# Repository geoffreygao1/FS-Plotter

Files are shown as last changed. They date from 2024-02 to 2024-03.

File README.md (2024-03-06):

# _F.S. PLOTTER_
**By: Geoffrey Gao**

<p align="center">

</p>

_An attachment for the [Ender 3](https://www.creality.com/products/ender-3-3d-printer) 3D Printer that allows for 2D Plotter functionality. This project was intended to allow for printing onto non-standard materials/objects. Included are the designs for the following:_

### Plotter

A spring loaded fixture to designed to hold a pen in place on the Ender 3 X-Carriage. Can be used with any writing utensil (up to 15mm diameter) and other tools (e.g., scribers, engravers, etc.)

<p align="center">
 <span>
  
</span>
</p>

### Cassette Tape Fixture
 A simple fixture to allow one to print directly onto a cassette tape. This was intended as a cheaper alternative to pad printing, with a better finish than printout tape labels. For best results, use an oil ink based pen for printing to prevent smearing. 

  <p align="center">
  <span>     
    </span>
  </p>

## Examples

Showcasing prints on paper, wood, fabric, cassette, and engraving on acrylic:
<p align="center">
<span>





</span>
</p>

## Getting Started

### Design Files
This repo contains design files for the main Plotter assembly and the Cassette Tape Fixture. The plotter was designed to be compatible with the Ender 3 X carriage. You can 3D print the STL files without the need for supports using your preferred slicer settings. There are also design templates included for use with the cassette fixture.

### PrusaSlicer Settings
The PrusaSlicer settings profile I use to generate the plotter GCode is included. PrusaSlicer is a free slicer available [here](https://www.prusa3d.com/en/page/prusaslicer_424/). You can learn how to import profile settings [here](https://help.prusa3d.com/article/how-to-import-and-export-custom-profiles-in-prusaslicer_382766). The input into PrusaSlicer will be the SVG file formats of your design.

### Instructions
Contains PDFs with instructions on how to assemble, install, and use the plotter. Also includes a disassembly guide on how to remove the existing hotend on the Ender 3 printer.

## Setup/Installation Requirements
### Tools
The following tools are needed to build the F.S. Plotter and Cassette Fixture:
*  Ender 3 3D Printer
*  Hex Drivers
*  M2, M3, M4 Thread Taps
*  Computer capable of running PrusaSlicer

### Materials
The following materials are needed to build the F.S. Plotter and Cassette Fixture 
_(Note the springs and screws are purchased in a kit but only specific ones are needed. See assembly instructions for details)_:
*  PLA to print the parts
*  [40mm Linear Rail](https://www.aliexpress.us/item/2251832805844953.html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)
* [Metric Screw Kit](https://www.amazon.com/gp/product/B07K141VFD/ref=ppx_yo_dt_b_search_asin_title?ie=UTF8&psc=1)
* [Extension Spring Kit](https://www.amazon.com/dp/B0CFRF42LQ?psc=1&ref=ppx_yo2ov_dt_b_product_details)
* [Compression Spring Kit](https://www.amazon.com/Dianrui-Compression-Assortment-Mechanical-K-P-051-300/dp/B0BVTDP29W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)

If individual parts are purchased separately (via Aliexpress), both assemblies can be built for around $30!

## Assembly/Usage Instructions
_Please see the PDFs included in the [Instructions Folder](https://github.com/geoffreygao1/Plotter/tree/main/Instructions) for assembly and usage instructions_

## Notes

This is still a work in progress so please check regularly for updates! Special thanks to Jake C. for allowing me to borrow his Ender 3!

## License
Copyright (c) _2024_  _Geoffrey Gao_  
_Not for commercial use_

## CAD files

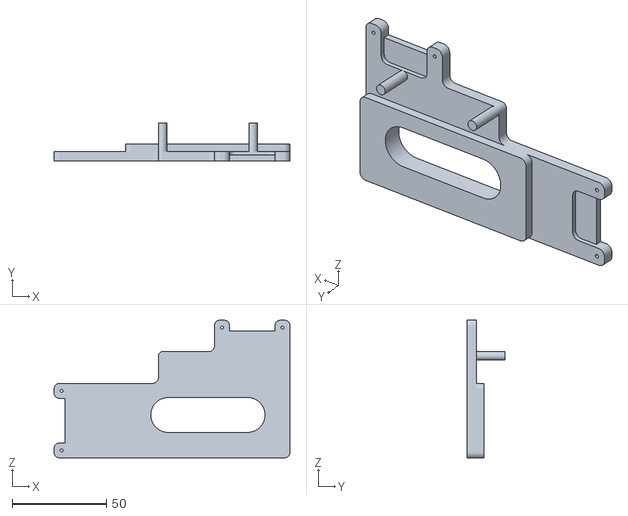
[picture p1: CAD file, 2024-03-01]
Design Files/Cassette Mount/Base, Cassette Fixture, V3.STL
125.0 x 20.0 x 73.0

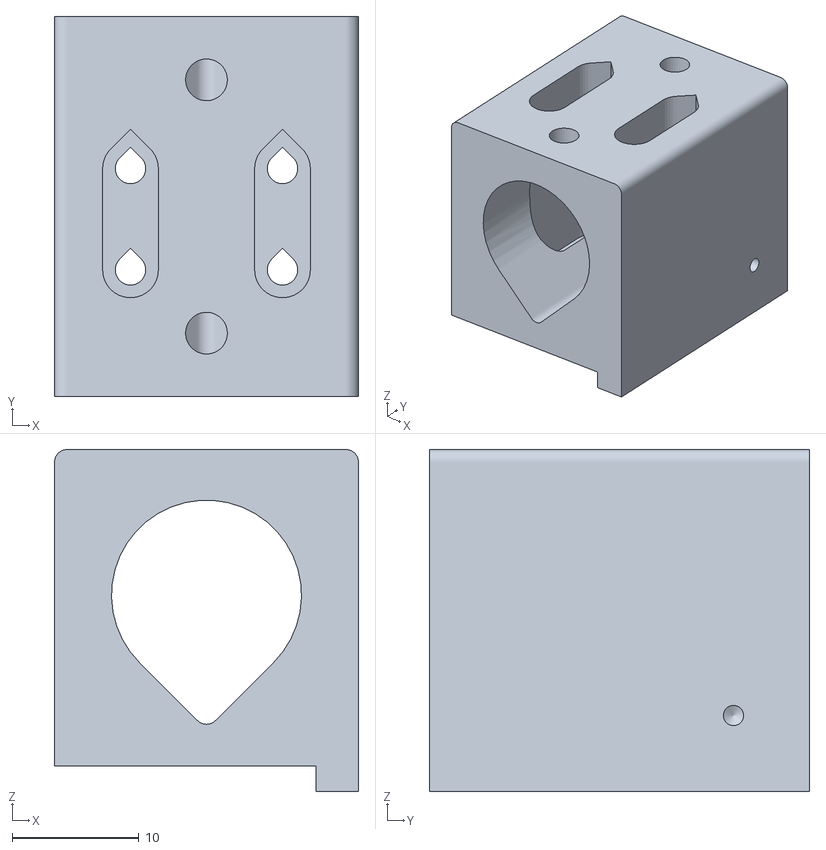
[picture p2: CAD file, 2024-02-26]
Design Files/Plotter/Carriage Mount.STL
24.0 x 30.0 x 27.0

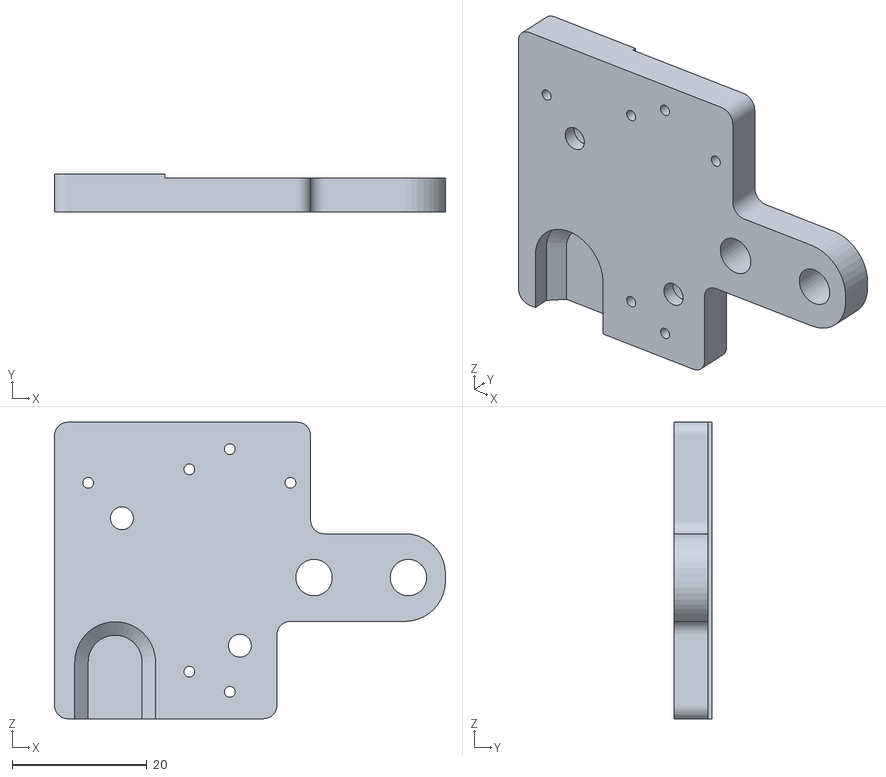
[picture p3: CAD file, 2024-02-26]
Design Files/Plotter/Pen Holder.STL
58.0 x 5.60 x 44.0

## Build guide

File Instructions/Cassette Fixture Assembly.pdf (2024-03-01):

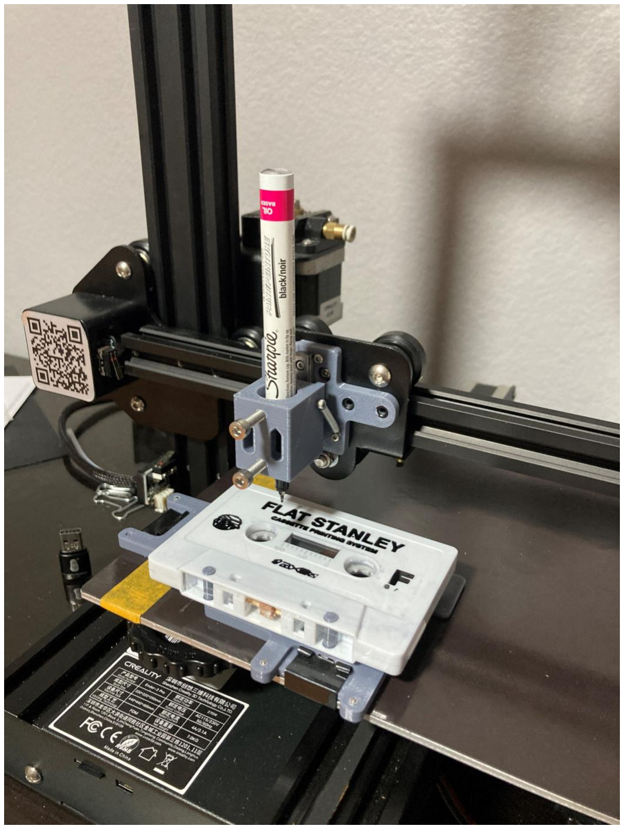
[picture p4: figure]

# Cassette Tape Fixture

Assembly / Installation Guide

By: Geoffrey Gao
02/2024

## Bill of Materials

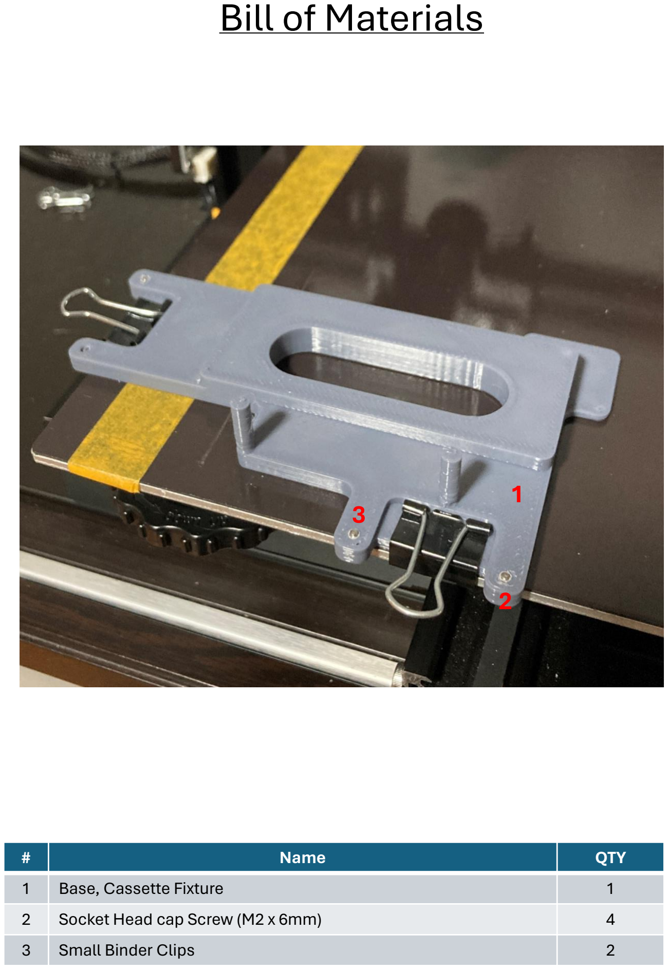
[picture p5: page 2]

# | Name | QTY

1 | Base, Cassette Fixture | 1
2 | Socket Head cap Screw (M2 x 6mm) | 4
3 | Small Binder Clips | 2

1

2

3

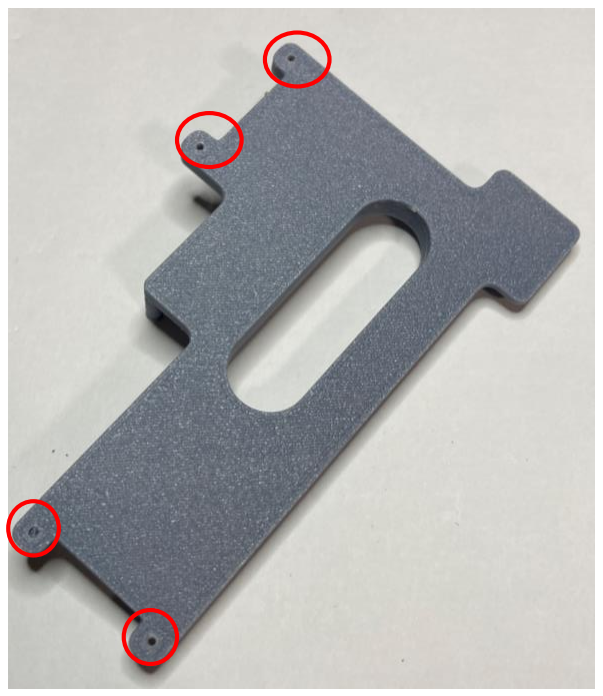
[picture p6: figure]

1. Tap the noted holes with an M2 Tap.

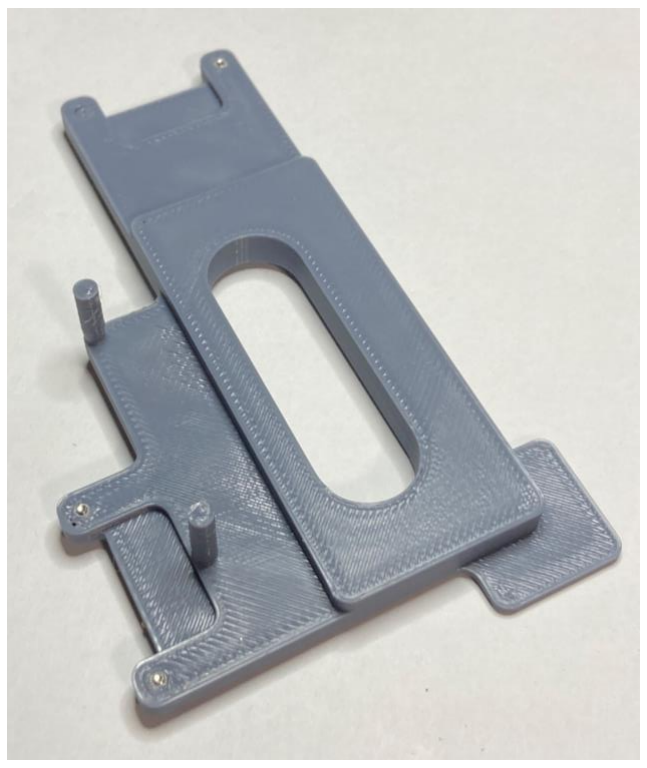
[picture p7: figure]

2. Install M2 x 6mm Screws in the holes that were just tapped from the bottom

## Assembly Instructions

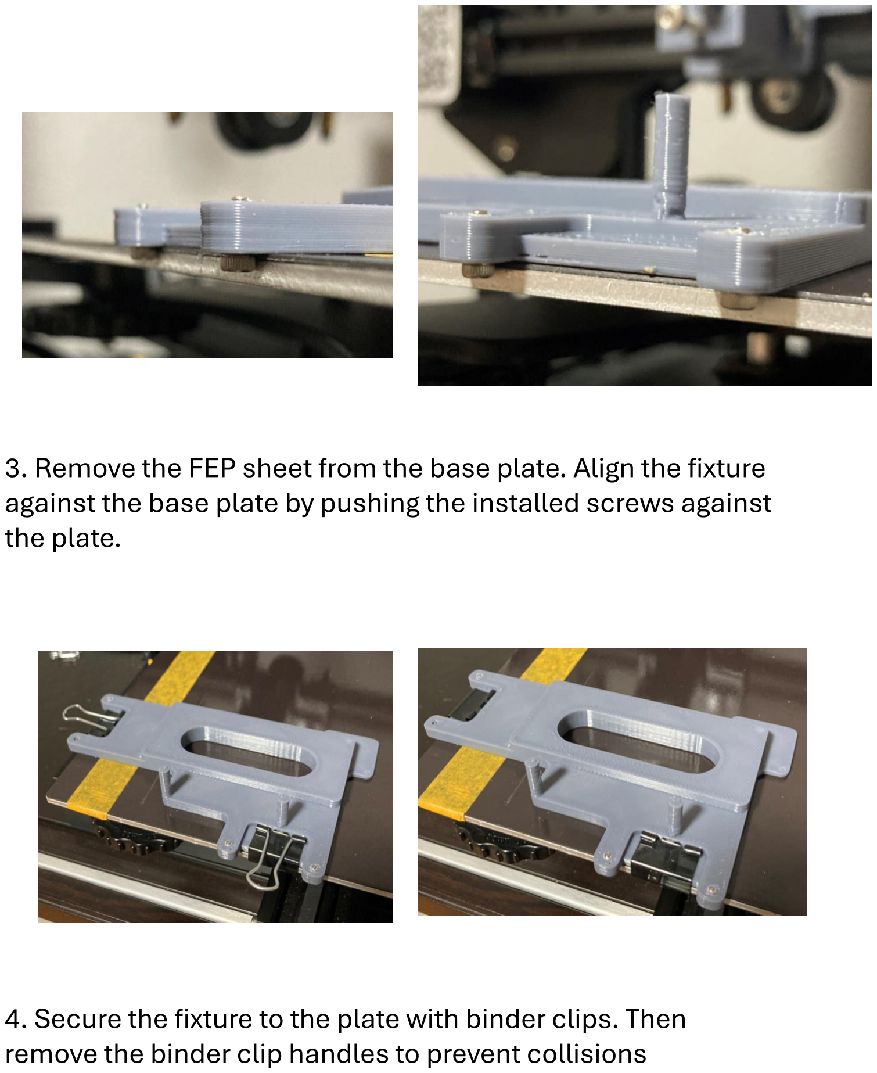
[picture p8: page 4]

3. Remove the FEP sheet from the base plate. Align the fixture against the base plate by pushing the installed screws against the plate.
4. Secure the fixture to the plate with binder clips. Then remove the binder clip handles to prevent collisions

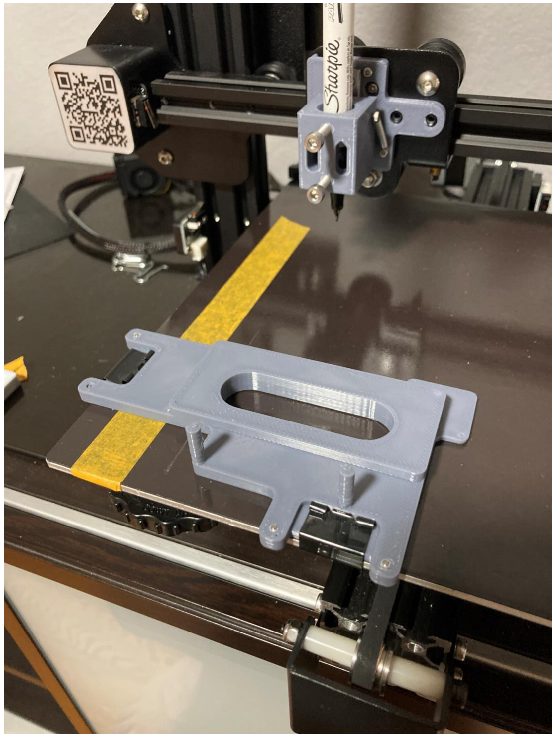
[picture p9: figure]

Installation is complete!

## Setup Instructions

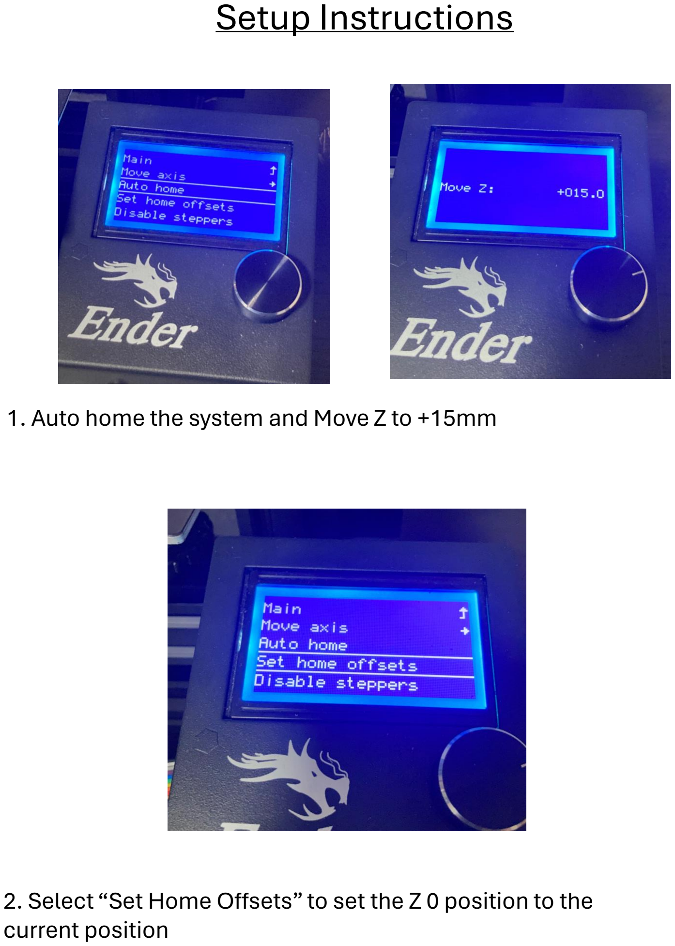
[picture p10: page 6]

1. Auto home the system and Move Z to +15mm
2. Select “Set Home Offsets” to set the Z 0 position to the current position

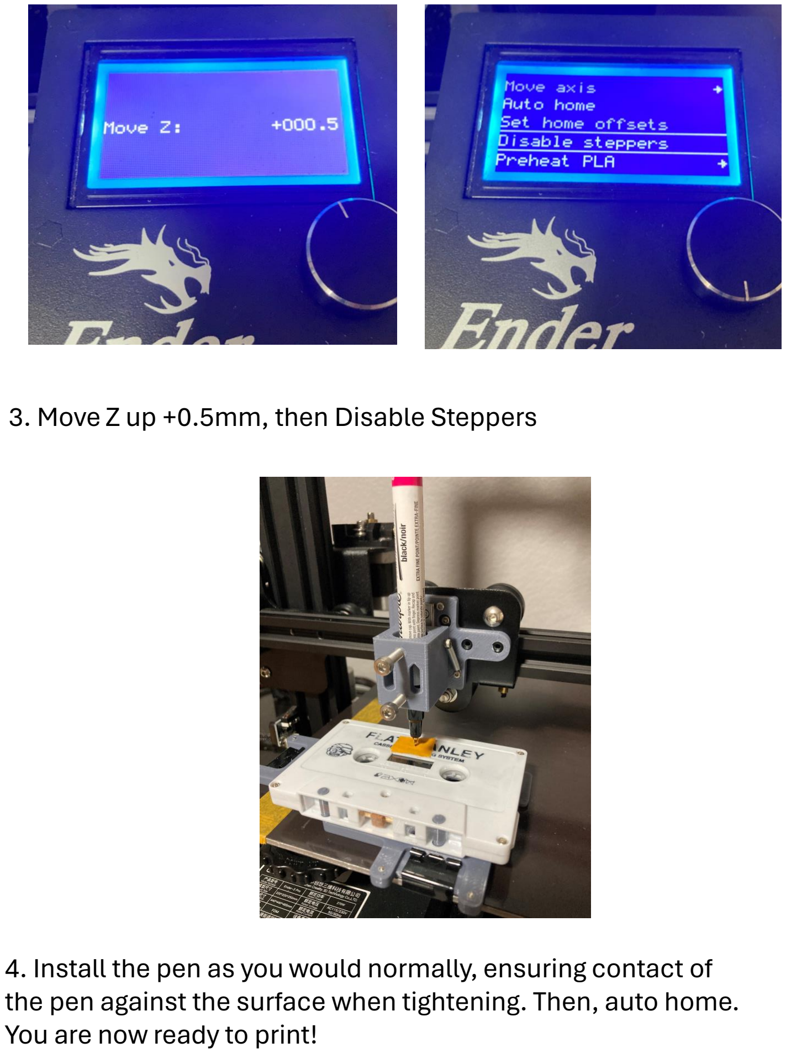
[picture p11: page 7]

3. Move Z up +0.5mm, then Disable Steppers
4. Install the pen as you would normally, ensuring contact of the pen against the surface when tightening. Then, auto home. You are now ready to print!

## Gcode Generation

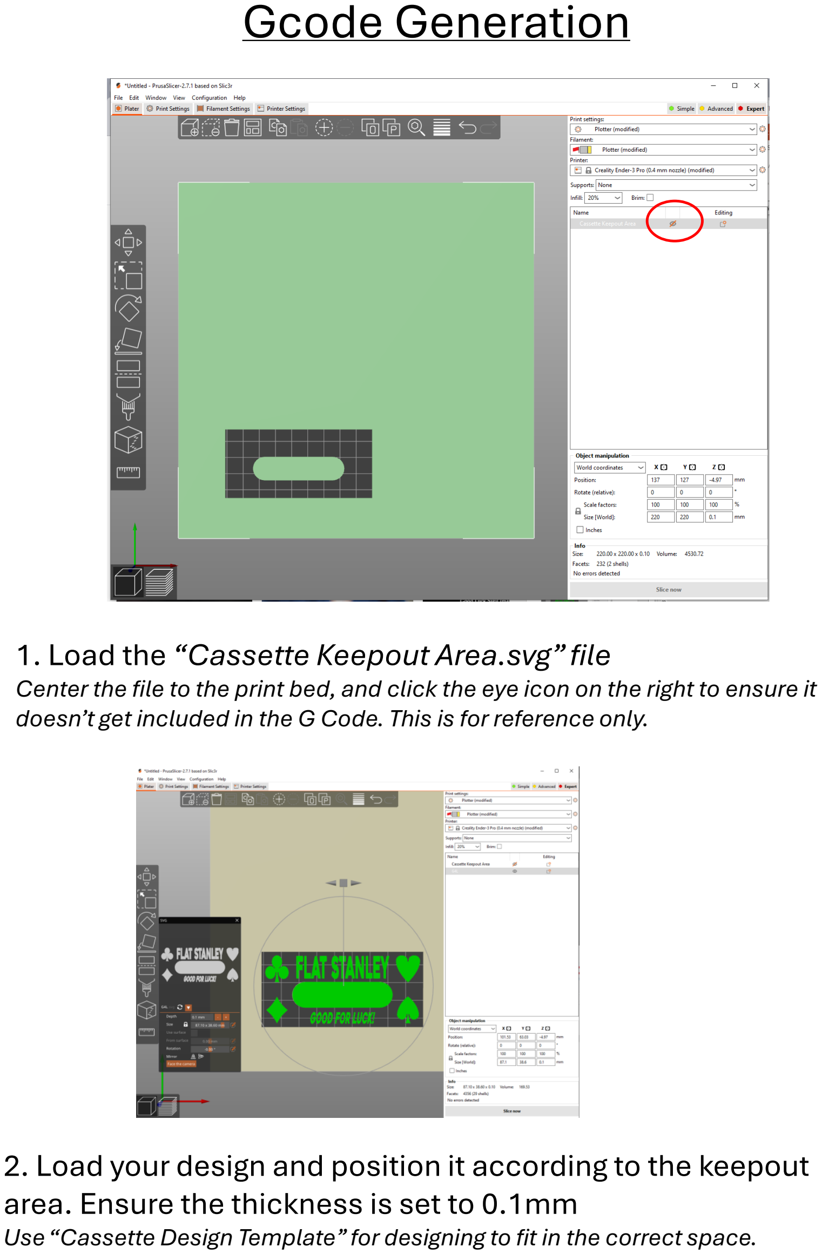
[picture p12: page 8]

1. Load the “Cassette Keepout Area.svg” file
Center the file to the print bed, and click the eye icon on the right to ensure it doesn’t get included in the G Code. This is for reference only.
2. Load your design and position it according to the keepout area. Ensure the thickness is set to 0.1mm
Use “Cassette Design Template” for designing to fit in the correct space.

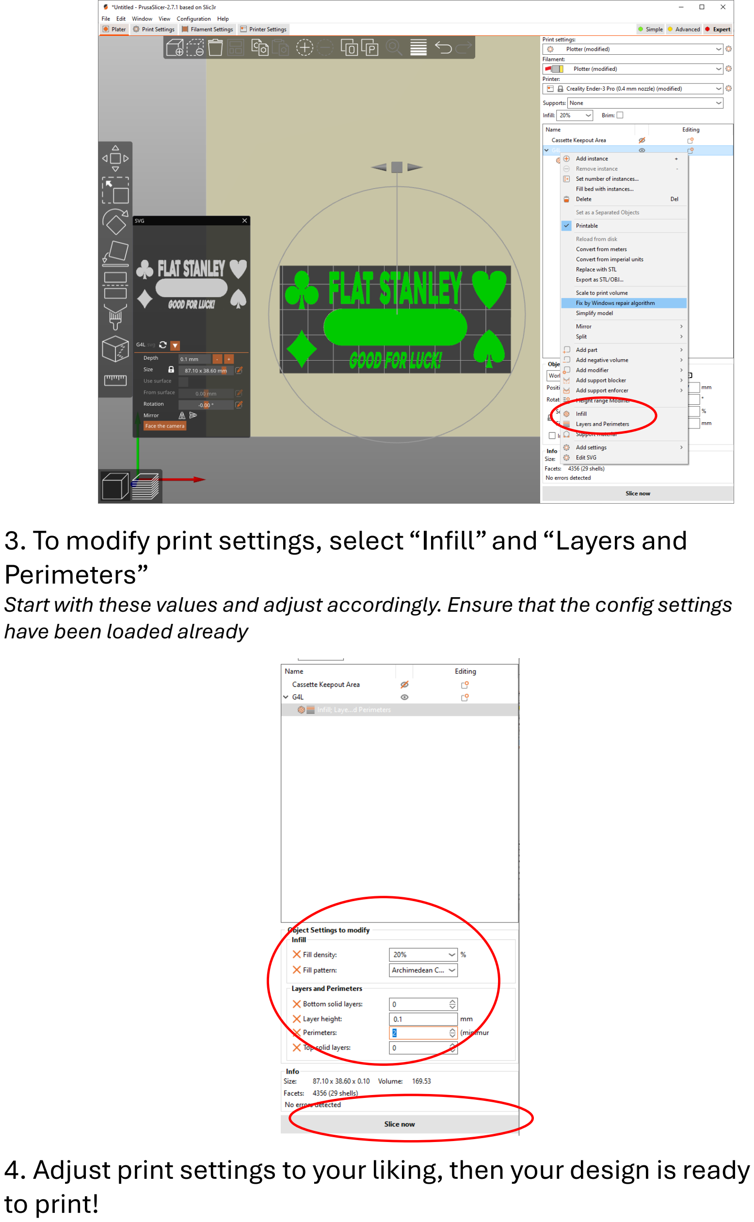
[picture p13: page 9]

3. To modify print settings, select “Infill” and “Layers and Perimeters”
Start with these values and adjust accordingly. Ensure that the config settings have been loaded already
4. Adjust print settings to your liking, then your design is ready to print!

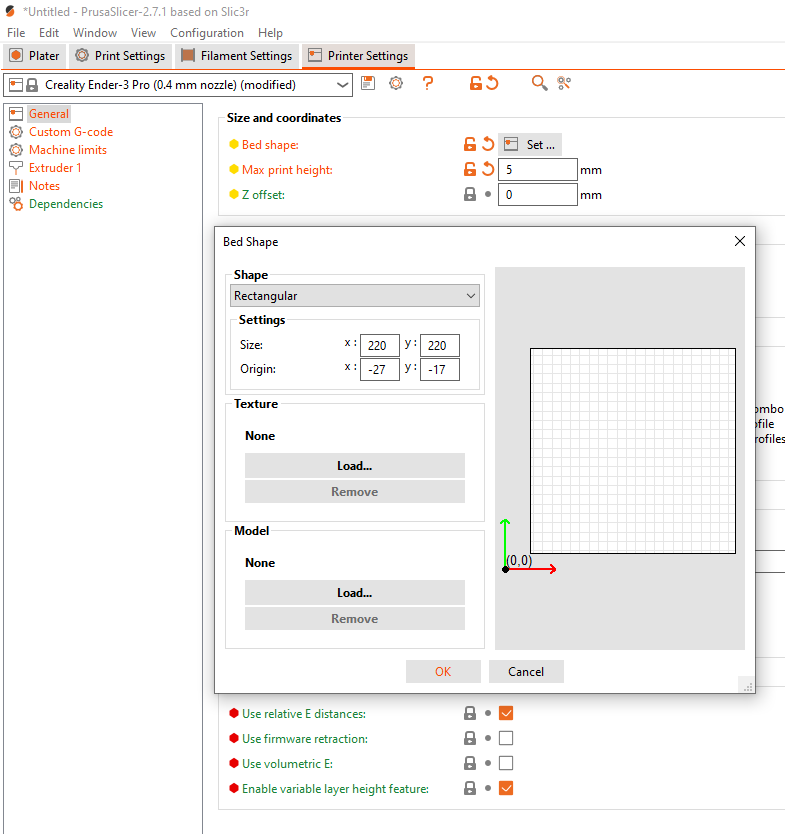
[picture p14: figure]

If you are noticing that the print is not aligned to the intended coordinates, you may have to adjust the XY offset in Prusaslicer
- In PrusaSlicer , Printer Settings, Bed Shape, and adjust the Origin XY values
- These values are related to the size of the pen being used, so adjust accordingly

Troubleshooting:

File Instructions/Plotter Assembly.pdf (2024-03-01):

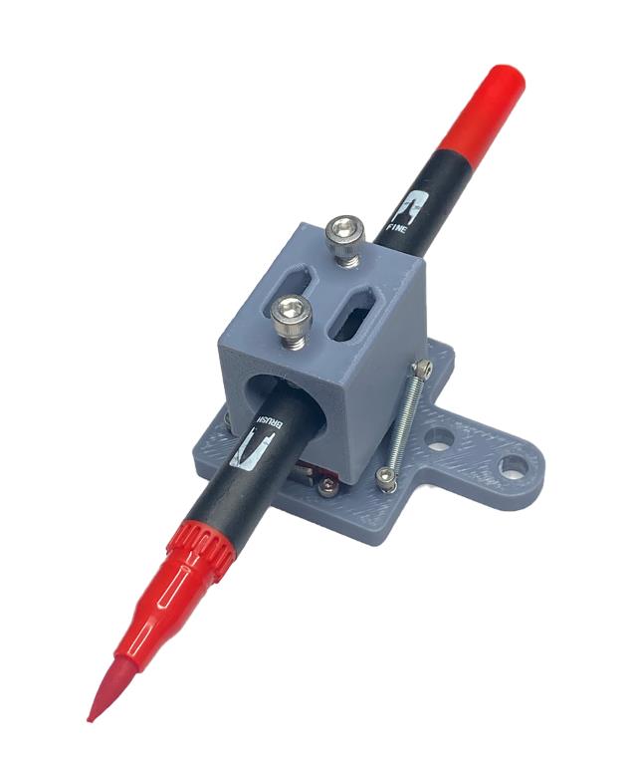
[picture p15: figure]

# FS Plotter

## Assembly / Installation Guide

By: Geoffrey Gao
02/2024

# Bill of Materials

3

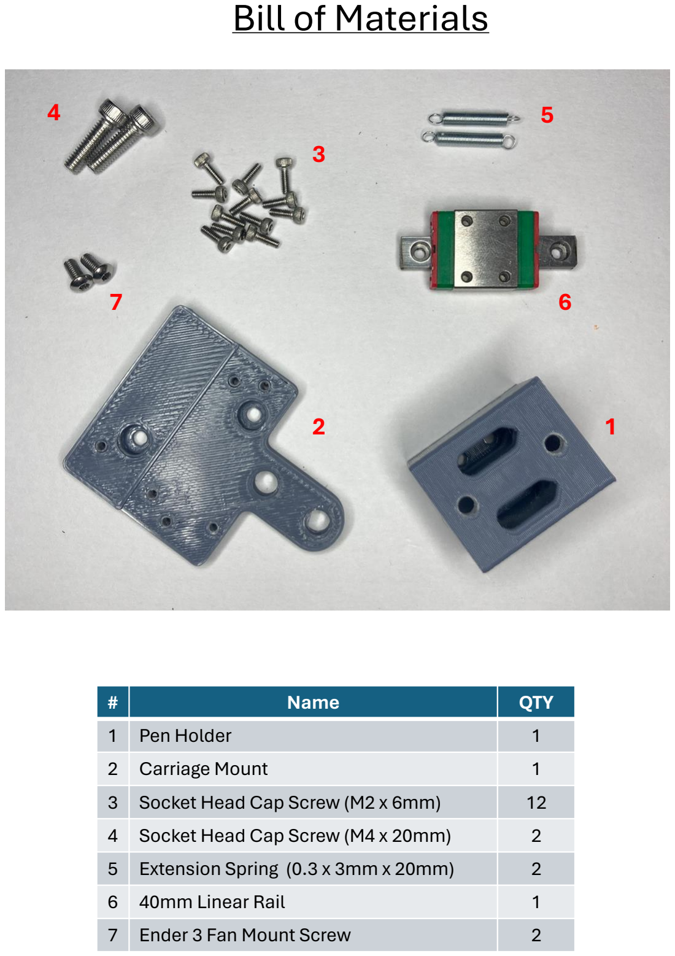
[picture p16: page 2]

# | Name | QTY

1 | Pen Holder | 1
2 | Carriage Mount | 1
3 | Socket Head Cap Screw (M2 x 6mm) | 12
4 | Socket Head Cap Screw (M4 x 20mm) | 2
5 | Extension Spring (0.3 x 3mm x 20mm) | 2
6 | 40mm Linear Rail | 1
7 | Ender 3 Fan Mount Screw | 2

2 1

4 5

7 6

# Assembly Instructions

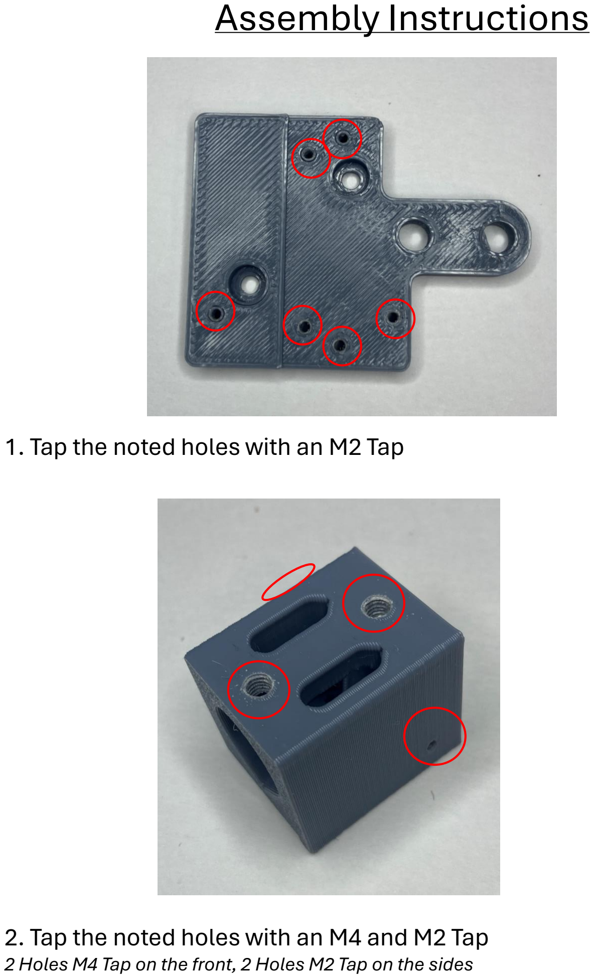
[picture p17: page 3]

### 1. Tap the noted holes with an M2 Tap

### 2. Tap the noted holes with an M4 and M2 Tap

2 Holes M4 Tap on the front, 2 Holes M2 Tap on the sides

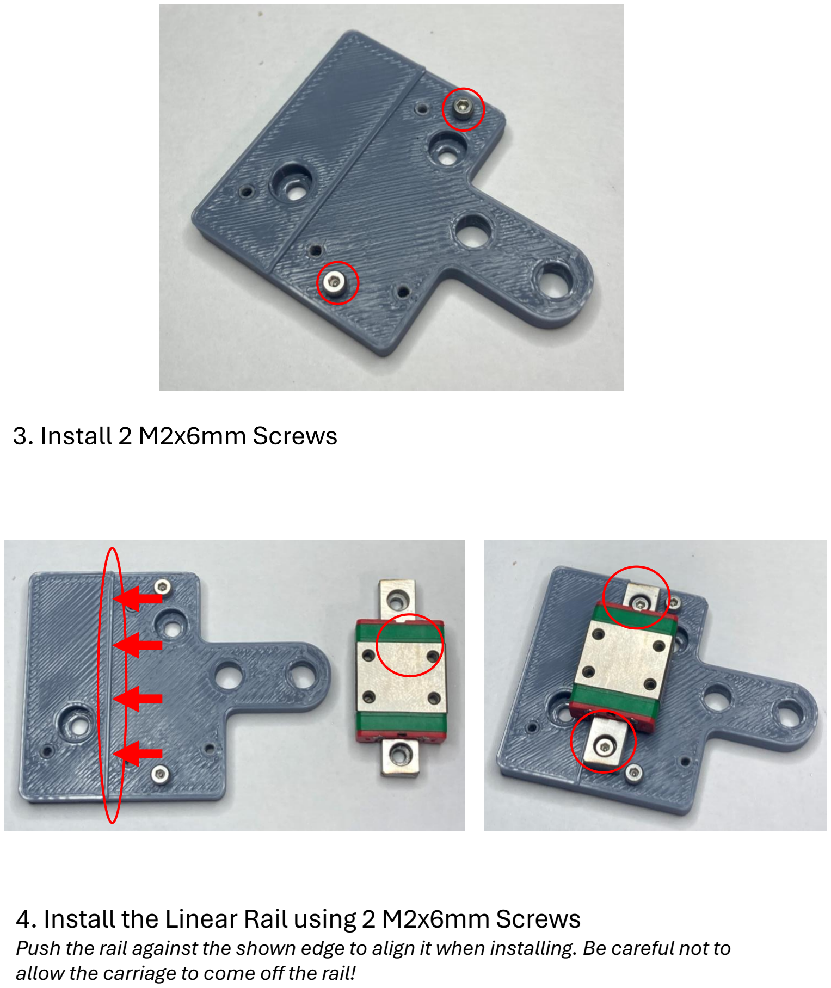
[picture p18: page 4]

### 3. Install 2 M2x6mm Screws

### 4. Install the Linear Rail using 2 M2x6mm Screws

Push the rail against the shown edge to align it when installing. Be careful not to allow the carriage to come off the rail!

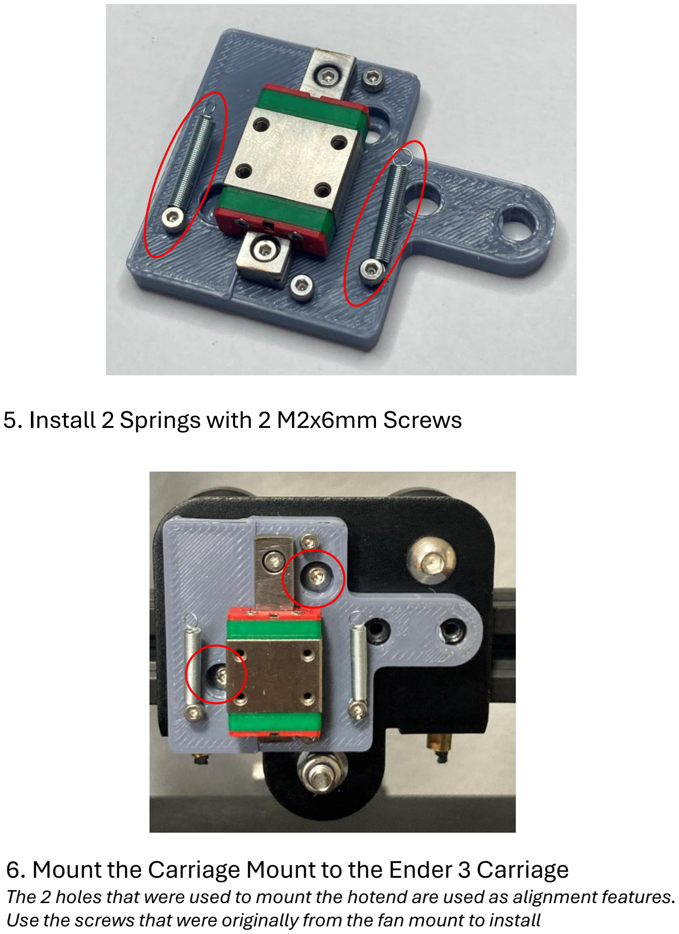
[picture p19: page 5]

### 5. Install 2 Springs with 2 M2x6mm Screws

### 6. Mount the Carriage Mount to the Ender 3 Carriage

The 2 holes that were used to mount the hotend are used as alignment features. Use the screws that were originally from the fan mount to install

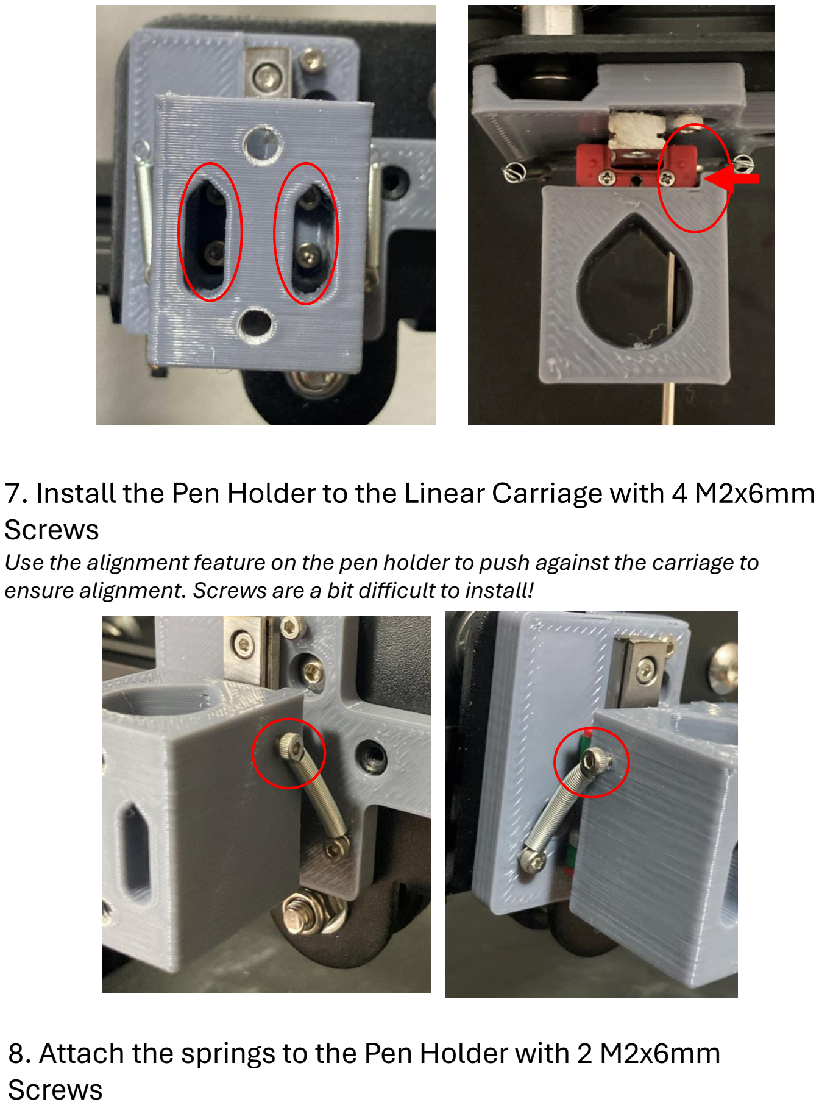
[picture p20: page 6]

### 7. Install the Pen Holder to the Linear Carriage with 4 M2x6mm Screws

Use the alignment feature on the pen holder to push against the carriage to ensure alignment. Screws are a bit difficult to install!

### 8. Attach the springs to the Pen Holder with 2 M2x6mm Screws

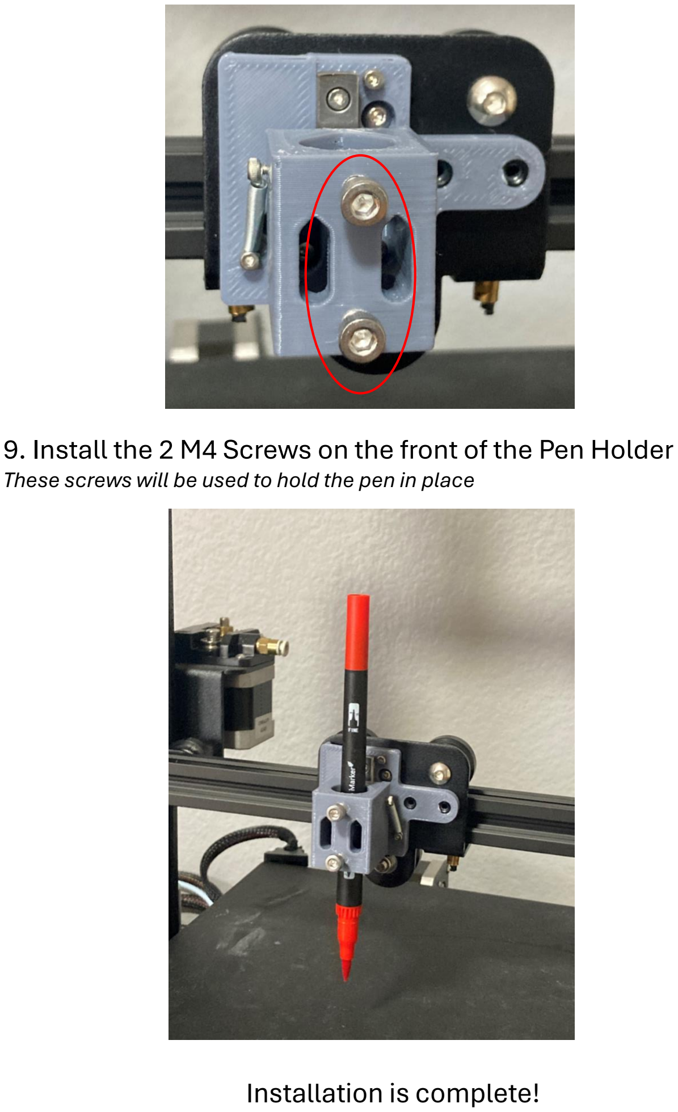
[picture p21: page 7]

### 9. Install the 2 M4 Screws on the front of the Pen Holder

These screws will be used to hold the pen in place

### Installation is complete!

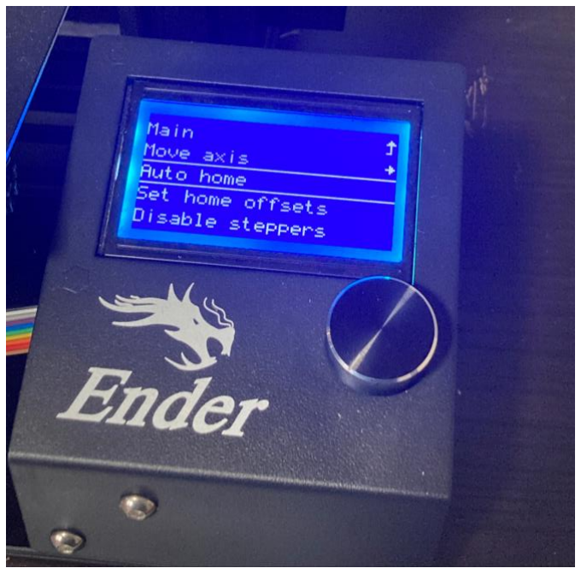
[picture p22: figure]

### 1. Auto home the printer

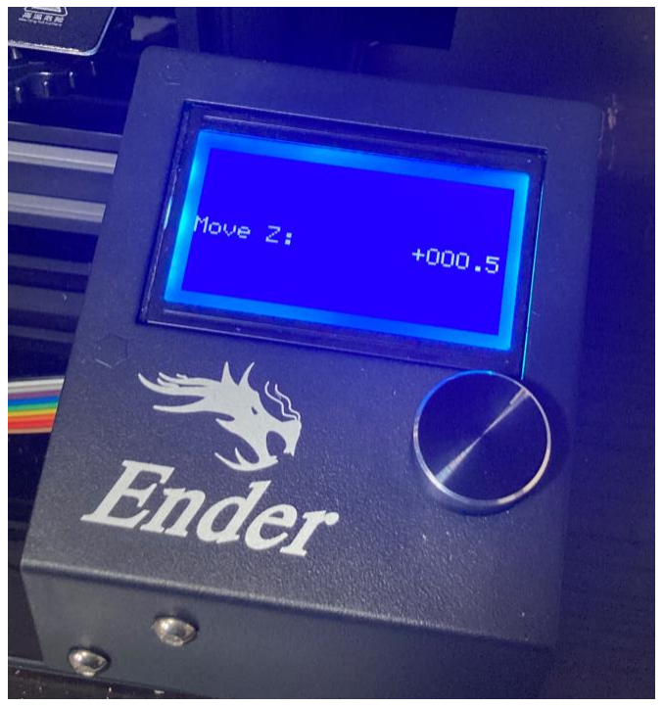
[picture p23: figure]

### 2. Move Z axis to 0.5mm

Depending on how precisely your bed is leveled, a smaller number can be used as long as it is greater than 0.1mm. I usually use 0.5mm to be safe

# Pen Height Calibration

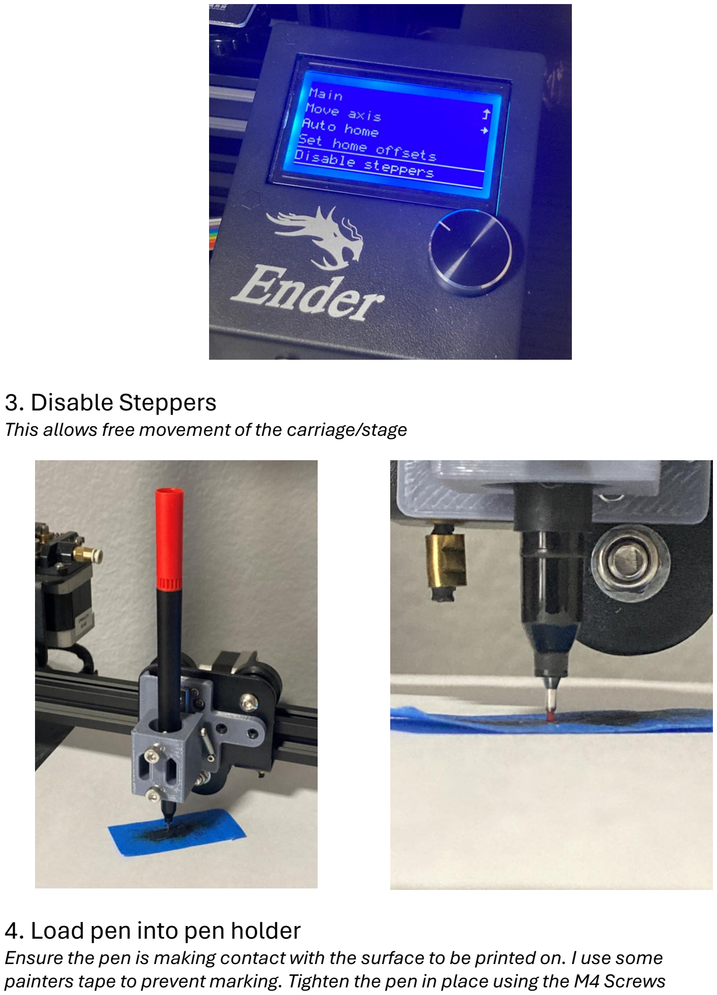
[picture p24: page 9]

### 3. Disable Steppers

This allows free movement of the carriage/stage

### 4. Load pen into pen holder

Ensure the pen is making contact with the surface to be printed on. I use some painters tape to prevent marking. Tighten the pen in place using the M4 Screws

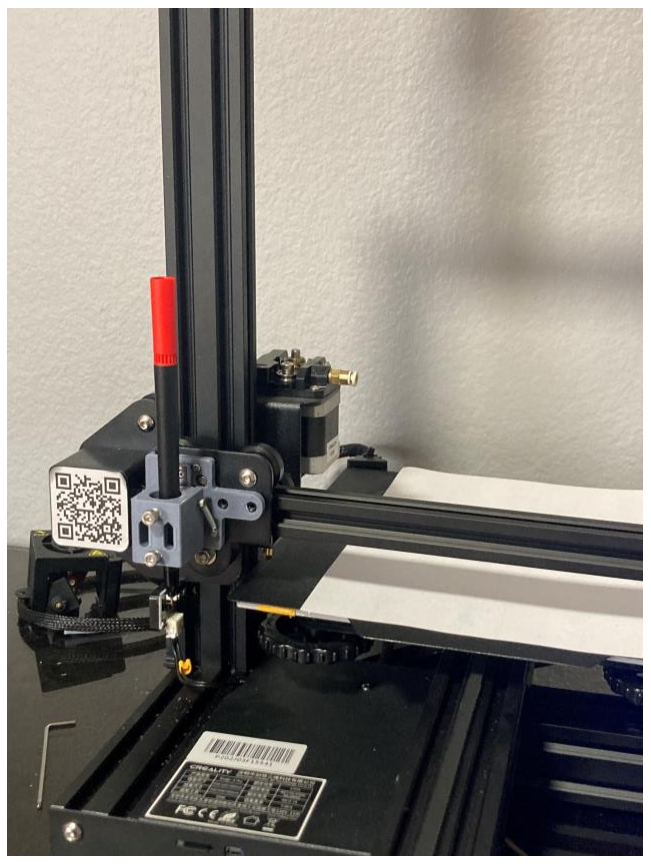
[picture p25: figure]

### 5. Auto Home the printer

The holder is ready to be used. Any time the pen is switched out, this process should be repeated.

# Gcode Generation

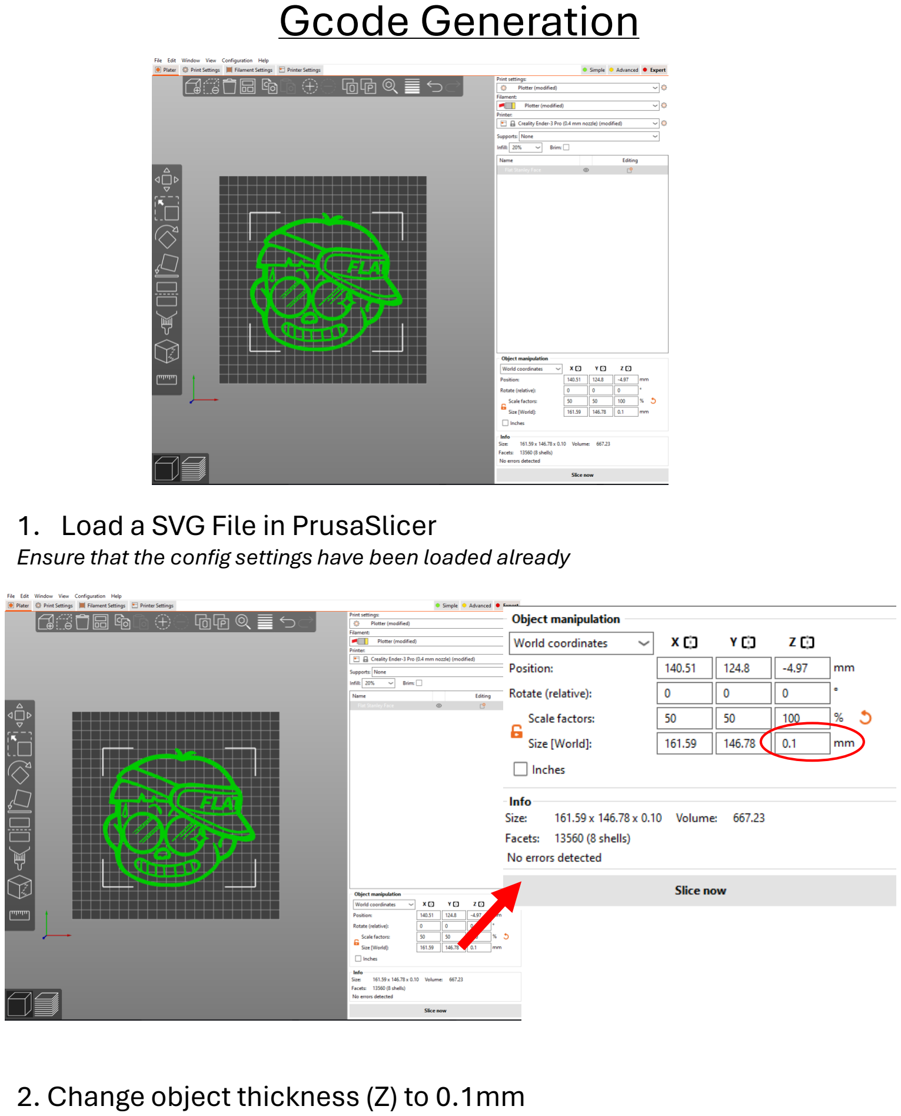
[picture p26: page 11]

### 1. Load a SVG File in PrusaSlicer

Ensure that the config settings have been loaded already

### 2. Change object thickness (Z) to 0.1mm

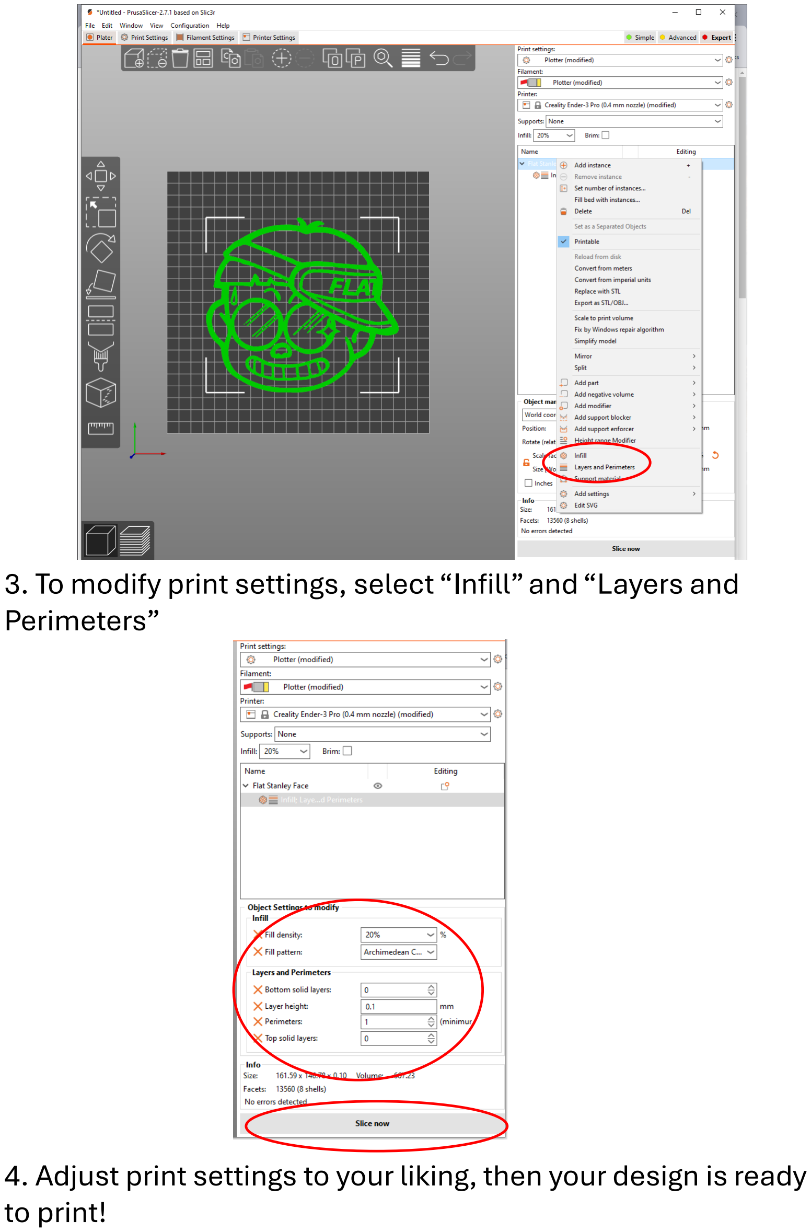
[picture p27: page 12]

### 3. To modify print settings, select “Infill” and “Layers and Perimeters”

### 4. Adjust print settings to your liking, then your design is ready to print!

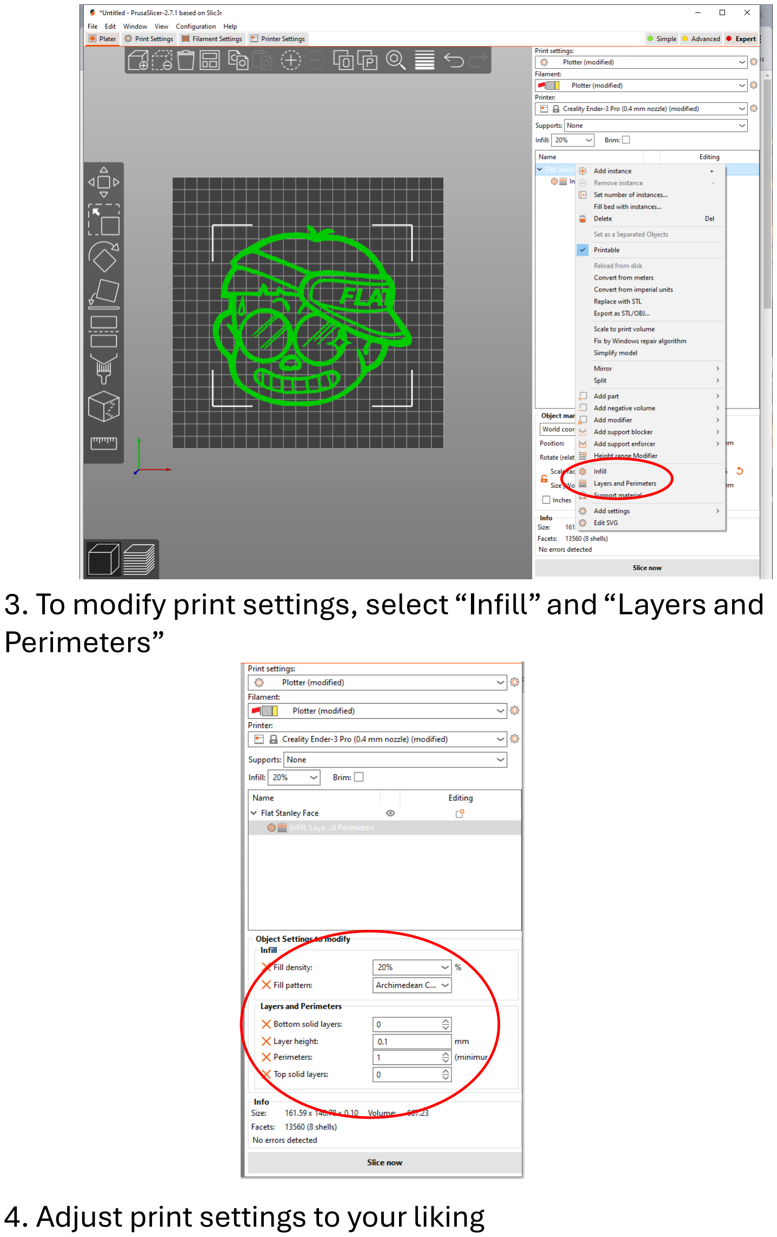
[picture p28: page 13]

### 3. To modify print settings, select “Infill” and “Layers and Perimeters”

### 4. Adjust print settings to your liking


### If you are noticing that the print is not aligned to the intended coordinates, you may have to adjust the XY offset in Prusaslicer

- In PrusaSlicer , Printer Settings, Bed Shape, and adjust the Origin XY values
- These values are related to the size of the pen being used, so adjust accordingly

### Troubleshooting:

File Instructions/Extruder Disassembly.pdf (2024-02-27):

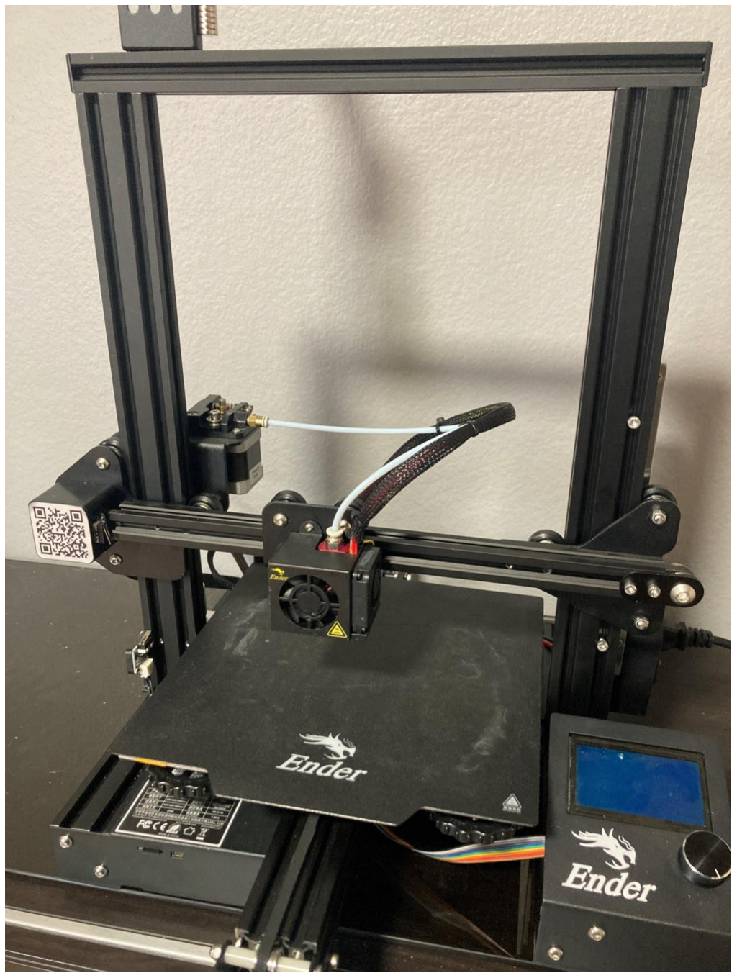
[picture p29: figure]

# CREALITY ENDER 3

## Extruder Disassembly Guide

By: Geoffrey Gao
02/2024

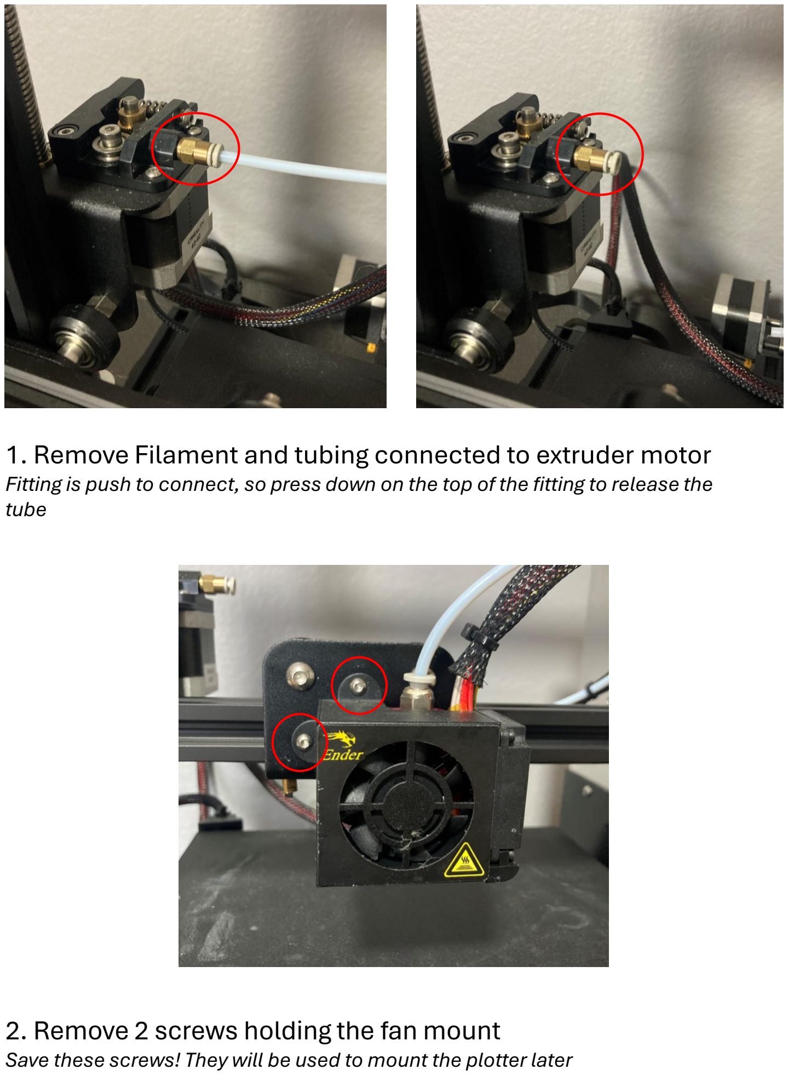
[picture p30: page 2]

### 1. Remove Filament and tubing connected to extruder motor

Fitting is push to connect, so press down on the top of the fitting to release the tube

### 2. Remove 2 screws holding the fan mount

Save these screws! They will be used to mount the plotter later

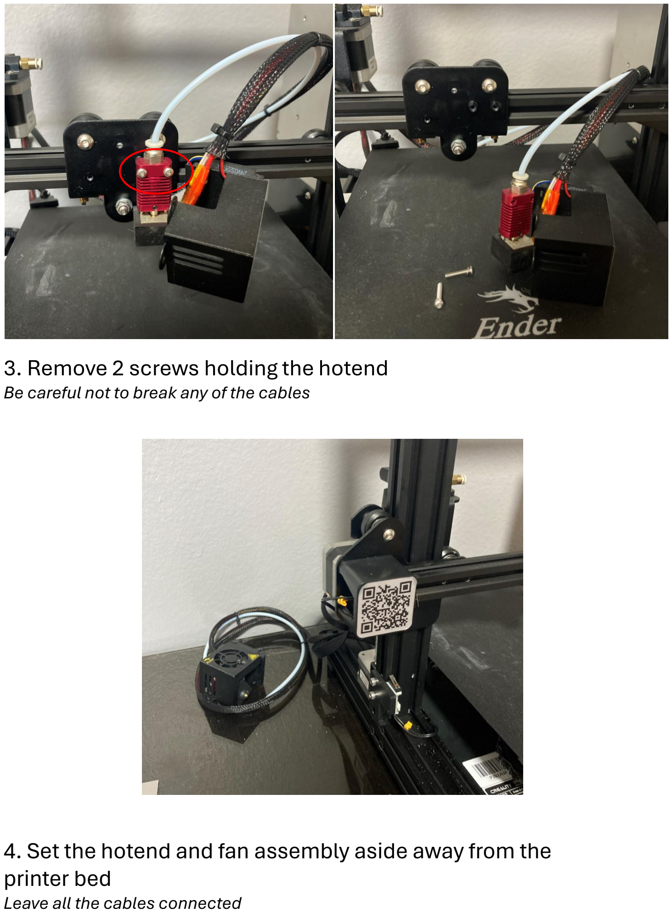
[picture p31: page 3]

### 3. Remove 2 screws holding the hotend

Be careful not to break any of the cables

### 4. Set the hotend and fan assembly aside away from the printer bed

Leave all the cables connected

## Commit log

2024-02-26 Added 3D files
    [Base, Cassette Fixture, V2.STL, Carriage Mount.STL, Holder, Cassette Fixture.STL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]
2024-02-26 Updated Casstte Fixture Base
    [Base, Cassette Fixture, V2.STL]
2024-02-26 Added Keepout Reference SVG
    [Keepout Reference.STL]
2024-02-27 Added Assembly Instructions
2024-02-28 Added instructions
    [Keepout Reference.STL]
2024-02-28 Removed keepout Reference
    [Keepout Reference.STL]
2024-02-29 Updated Cassette Mount
    [Base, Cassette Fixture, V2.STL, Base, Cassette Fixture, V3.STL, Holder, Cassette Fixture.STL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]
2024-02-29 removed old cassette fixture assembly
2024-03-01 Updated Instructions
    [Base, Cassette Fixture, V3.STL, Carriage Mount.STL, Pen Holder.STL]
2024-03-01 Removed magnet flange
    [Base, Cassette Fixture, V3.STL]
